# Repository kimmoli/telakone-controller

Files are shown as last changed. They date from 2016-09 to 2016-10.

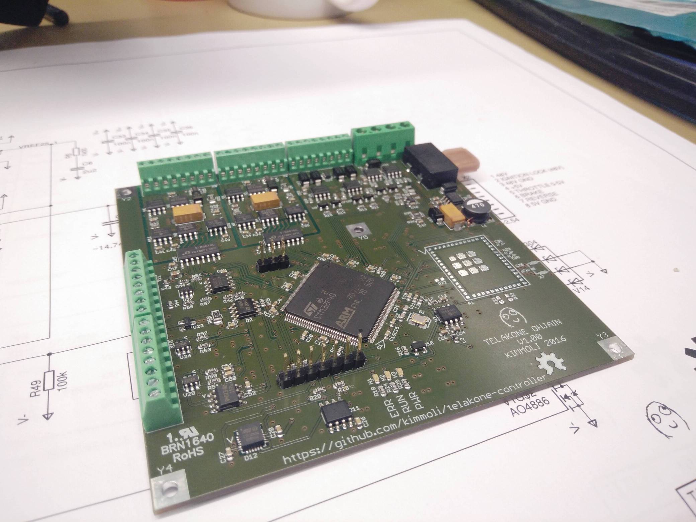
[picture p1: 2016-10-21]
docs/board.jpg

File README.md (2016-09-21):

telakone-controller
===================

STM32F407ZG + CC3100MOD WiFi with external antenna

12V to 3.3V switch mode power supply

Full bridge motor control with current measurement

4x high-side outputs
* PWM capable
* +12V, few amps

Dual isolated eBike motor control
* Throttle control (0-5V output)
* Brake and Reverse (low-side outputs)
* +48V voltage measurement

+12V supply voltage measurement

Temperature sensor

3-Axis accelerometer

Joystick input
* 2 potentiometers
* 2 buttons

Speed sensor inputs
* 2 channels
* for MLX90217 gear tooth sensor

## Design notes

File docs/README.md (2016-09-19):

Documentation
=============

All these are currently propably out of date, just showing off progress.

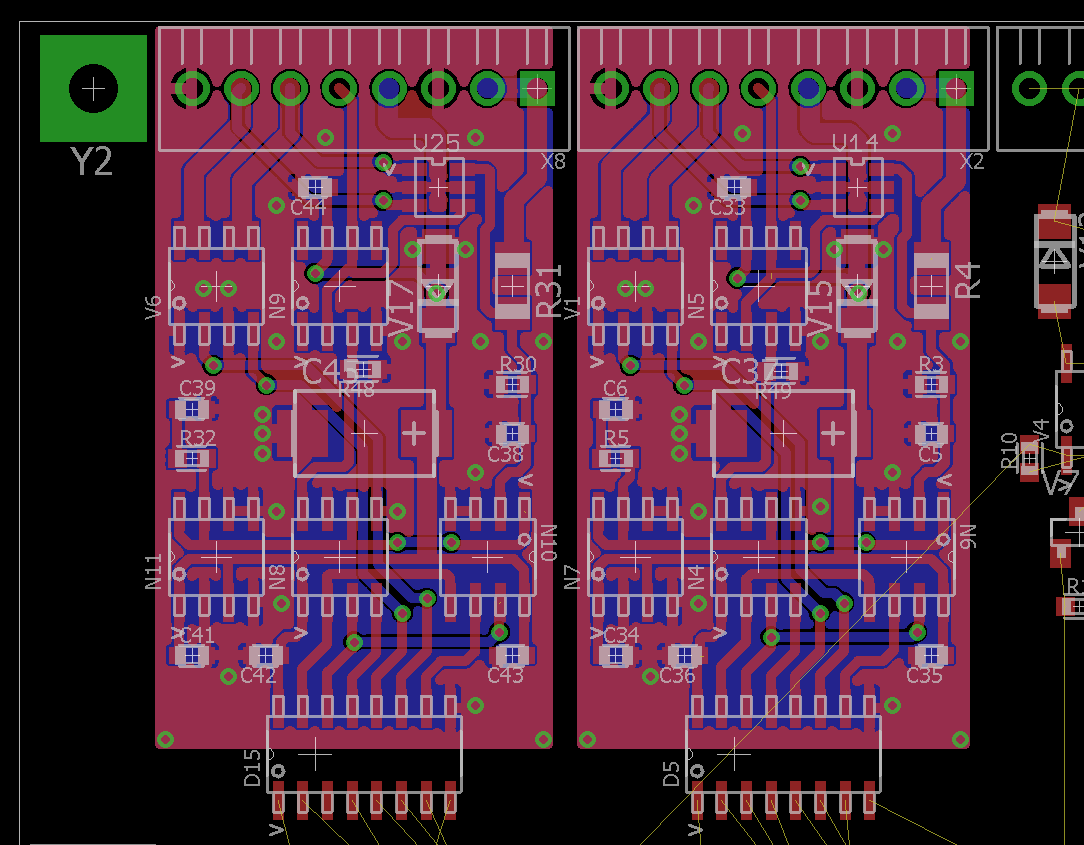
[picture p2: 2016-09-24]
docs/isolaatioryhma-sijoittelu.png

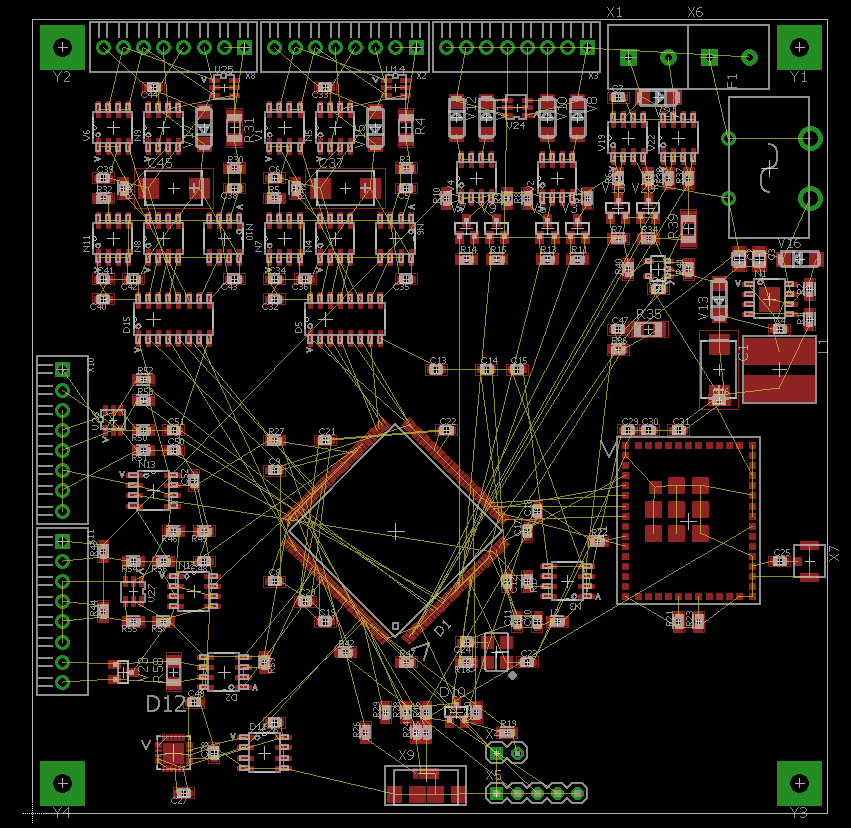
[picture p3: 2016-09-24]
docs/sijoittelu.png

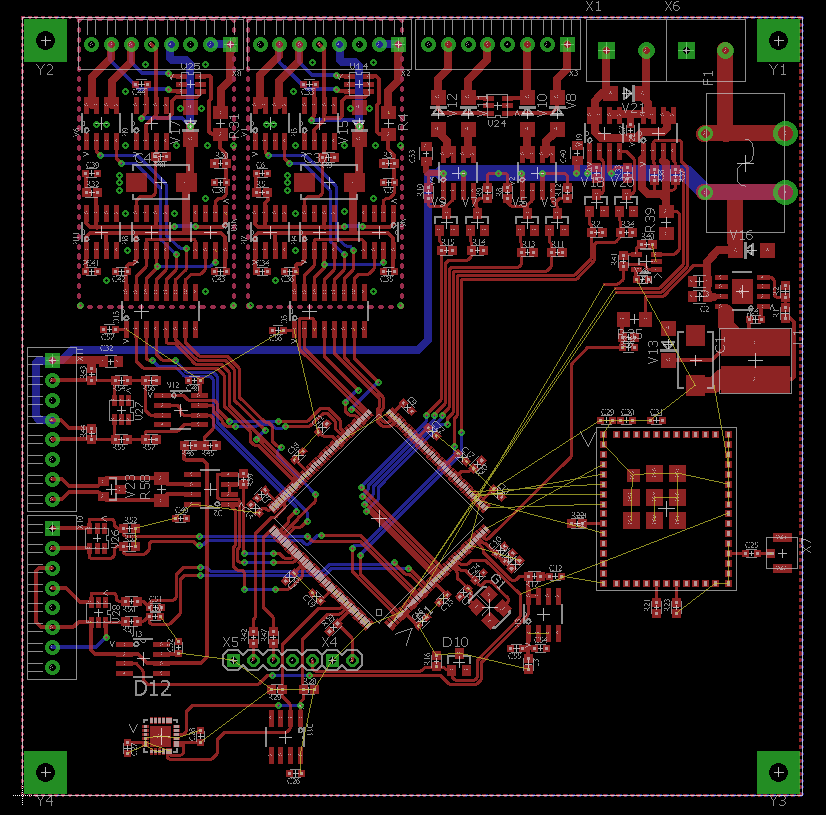
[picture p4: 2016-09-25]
docs/routtausta.png

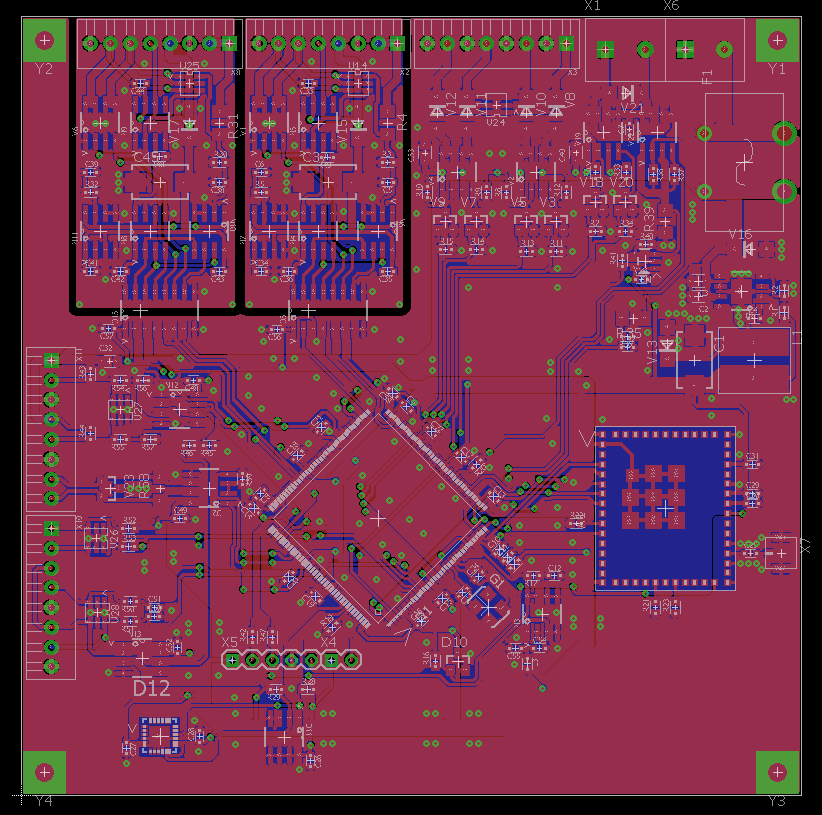
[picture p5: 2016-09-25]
docs/routattu.png

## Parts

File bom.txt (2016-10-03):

Partlist exported from c:/work/OMAT/telakone/telakone.sch at 3.10.2016 20:16

Qty Value           Device          Package               Parts                                                                                                                                                Description                          
2                   TE_RUUVILIITIN2 TE_RUUVILIITIN2       X1, X6                                                                                                                                                                                    
1   10              RES0603         R0603                 R40                                                                                                                                                                                       
2   100k            RES0603         R0603                 R48, R49                                                                                                                                                                                  
30  100n            CAP0603         C0603                 C10, C13, C14, C15, C16, C17, C18, C19, C20, C21, C22, C26, C27, C31, C33, C34, C35, C36, C41, C42, C43, C44, C46, C48, C49, C52, C55, C56, C57, C58                                      
1   10k0            RES0603         R0603                 R1                                                                                                                                                                                        
7   10n             CAP0603         C0603                 C4, C5, C7, C38, C47, C50, C51                                                                                                                                                            
1   10p             CAP0603         C0603                 C25                                                                                                                                                                                       
1   121 1206        RES1206         R1206                 R58                                                                                                                                                                                       
2   19k1 1206       RES1206         R1206                 R4, R31                                                                                                                                                                                   
5   1k00            RES0603         R0603                 R5, R17, R32, R43, R44                                                                                                                                                                    
3   220u 16V D      CPOL-EUCT7343   CT7343                C1, C37, C45                                                                                                                                         POLARIZED CAPACITOR, European symbol 
2   22p             CAP0603         C0603                 C23, C24                                                                                                                                                                                  
1   25MHz           XTAL_3225_SMD   X_3225                G1                                                                                                                                                   CRYSTAL CLOCK OSCILLATORS            
6   2N7002K         2N7002K         SOT23                 V3, V5, V7, V9, V18, V20                                                                                                                                                                  
26  2k00            RES0603         R0603                 R6, R7, R8, R9, R10, R11, R12, R13, R14, R15, R16, R19, R20, R21, R22, R23, R28, R29, R33, R34, R37, R38, R46, R52, R53, R59                                                              
10  2u2             CAP0603         C0603                 C6, C8, C9, C11, C12, C28, C29, C30, C39, C54                                                                                                                                             
5   2u2 50V 0805    CAP0805         C0805                 C2, C3, C32, C40, C53                                                                                                                                                                     
2   30k1            RES0603         R0603                 R54, R55                                                                                                                                                                                  
9   499             RES0603         R0603                 R18, R24, R25, R41, R42, R45, R47, R50, R51                                                                                                                                               
3   5k90            RES0603         R0603                 R2, R56, R57                                                                                                                                                                              
1   5k90 1206       RES1206         R1206                 R35                                                                                                                                                                                       
3   825             RES0603         R0603                 R3, R30, R36                                                                                                                                                                              
3   AO4803A         AO4803A         SOIC8-N_MC            V2, V4, V19                                                                                                                                                                               
3   AO4886          AO4886          SOIC8-N_MC            V1, V6, V22                                                                                                                                                                               
1   AZV3002S        AZV3002S        SOIC8-N_MC            N12                                                                                                                                                                                       
1   CC3100MOD       CC3100MOD       CC3100MOD             A1                                                                                                                                                                                        
8   DAFUG           DAFUG           DAFUG                 U$1, U$3, U$5, U$7, U$9, U$11, U$13, U$15                                                                                                                                                 
1   ERJ-8BWFR010V   RES1206         R1206                 R39                                                                                                                                                                                       
2   ESDA19SC6       ESDAXXSC6       SOT23-6               V24, V27                                                                                                                                                                                  
2   GRN             LEDCHIP-LED0603 CHIP-LED0603          H2, H3                                                                                                                                               LED                                  
1   IIS328DQTR      IIS328DQTR      QFN50P400X400X100-25N D12                                                                                                                                                                                       
2   IND0603         IND0603         R0603                 L2, L3                                                                                                                                                                                    
1   KEYSTONE-3549-2 KEYSTONE-3549-2 KEYSTONE-3549-2       F1                                                                                                                                                                                        
1   LM75BD          LM75BD          SOIC8-N_MC            D11                                                                                                                                                                                       
1   LTC2050CS5      LTC2050CS5      SOT95P280X145-5N      N2                                                                                                                                                                                        
1   MAX3430_SA      MAX3088_SA      SOIC8-N_MC            D2                                                                                                                                                                                        
3   MCP1501/SN      MCP1501/SN      SOIC8-N_MC            N3, N7, N11                                                                                                                                                                               
2   MCP3201/SN      MCP3201/SN      SOIC8-N_MC            N6, N10                                                                                                                                                                                   
2   MCP4921/SN      MCP4921/SN      SOIC8-N_MC            N4, N8                                                                                                                                                                                    
5   MPT0.5/8-2.54   MPT0.5/8-2.54   MPT0.5/8-2.54         X2, X3, X8, X10, X11                                                                                                                                                                      
1   PIIKKIRIMA-2    PIIKKIRIMA-2    PIIKKIRIMA-2          X4                                                                                                                                                                                        
1   PIIKKIRIMA-3    PIIKKIRIMA-3    PIIKKIRIMA-3          X9                                                                                                                                                                                        
1   PIIKKIRIMA-5    PIIKKIRIMA-5    PIIKKIRIMA-5          X5                                                                                                                                                                                        
5   PTH2.6-5.5SQ    PTH2.6-5.5SQ    PTH-2.6-5.5SQ         Y1, Y2, Y3, Y4, Y5                                                                                                                                                                        
1   RED             LEDCHIP-LED0603 CHIP-LED0603          H1                                                                                                                                                   LED                                  
1   RT9818C-29GV    RT9818C-29GV    SOT23                 D10                                                                                                                                                                                       
2   SI8661-IS1      SI8661-IS1      SOIC16-N              D5, D15                                                                                                                                                                                   
5   SK34A           SK34A           DO214AC               V8, V10, V11, V12, V13                                                                                                                                                                    
1   SM712           SM712           SOT23                 V23                                                                                                                                                                                       
1   SMAJ20A         SMAJXXA         DO214AC               V16                                                                                                                                                                                       
1   SMAJ20CA        SMAJXXCA        DO214AC               V21                                                                                                                                                                                       
2   SMAJ5.0A        SMAJXXA         DO214AC               V15, V17                                                                                                                                                                                  
1   STM32F407ZG     STM32F407ZG     LQFP-144              D1                                                                                                                                                                                        
1   TPS5430DDA      TPS5430DDA      SOIC8-N-EP            N1                                                                                                                                                                                        
3   TS921IDT        TS921IDT        SOIC8-N_MC            N5, N9, N13                                                                                                                                                                               
1   U.FL-R-SMT-1    U.FL-R-SMT-1    U.FL-R-SMT-1          X7                                                                                                                                                                                        
1   VLP8040-47U     VLP8040-47U     VLP8040               L1                                                                                                                                                                                        
4   WURTH 82402304  ESDAXXSC6       SOT23-6               V14, V25, V26, V28

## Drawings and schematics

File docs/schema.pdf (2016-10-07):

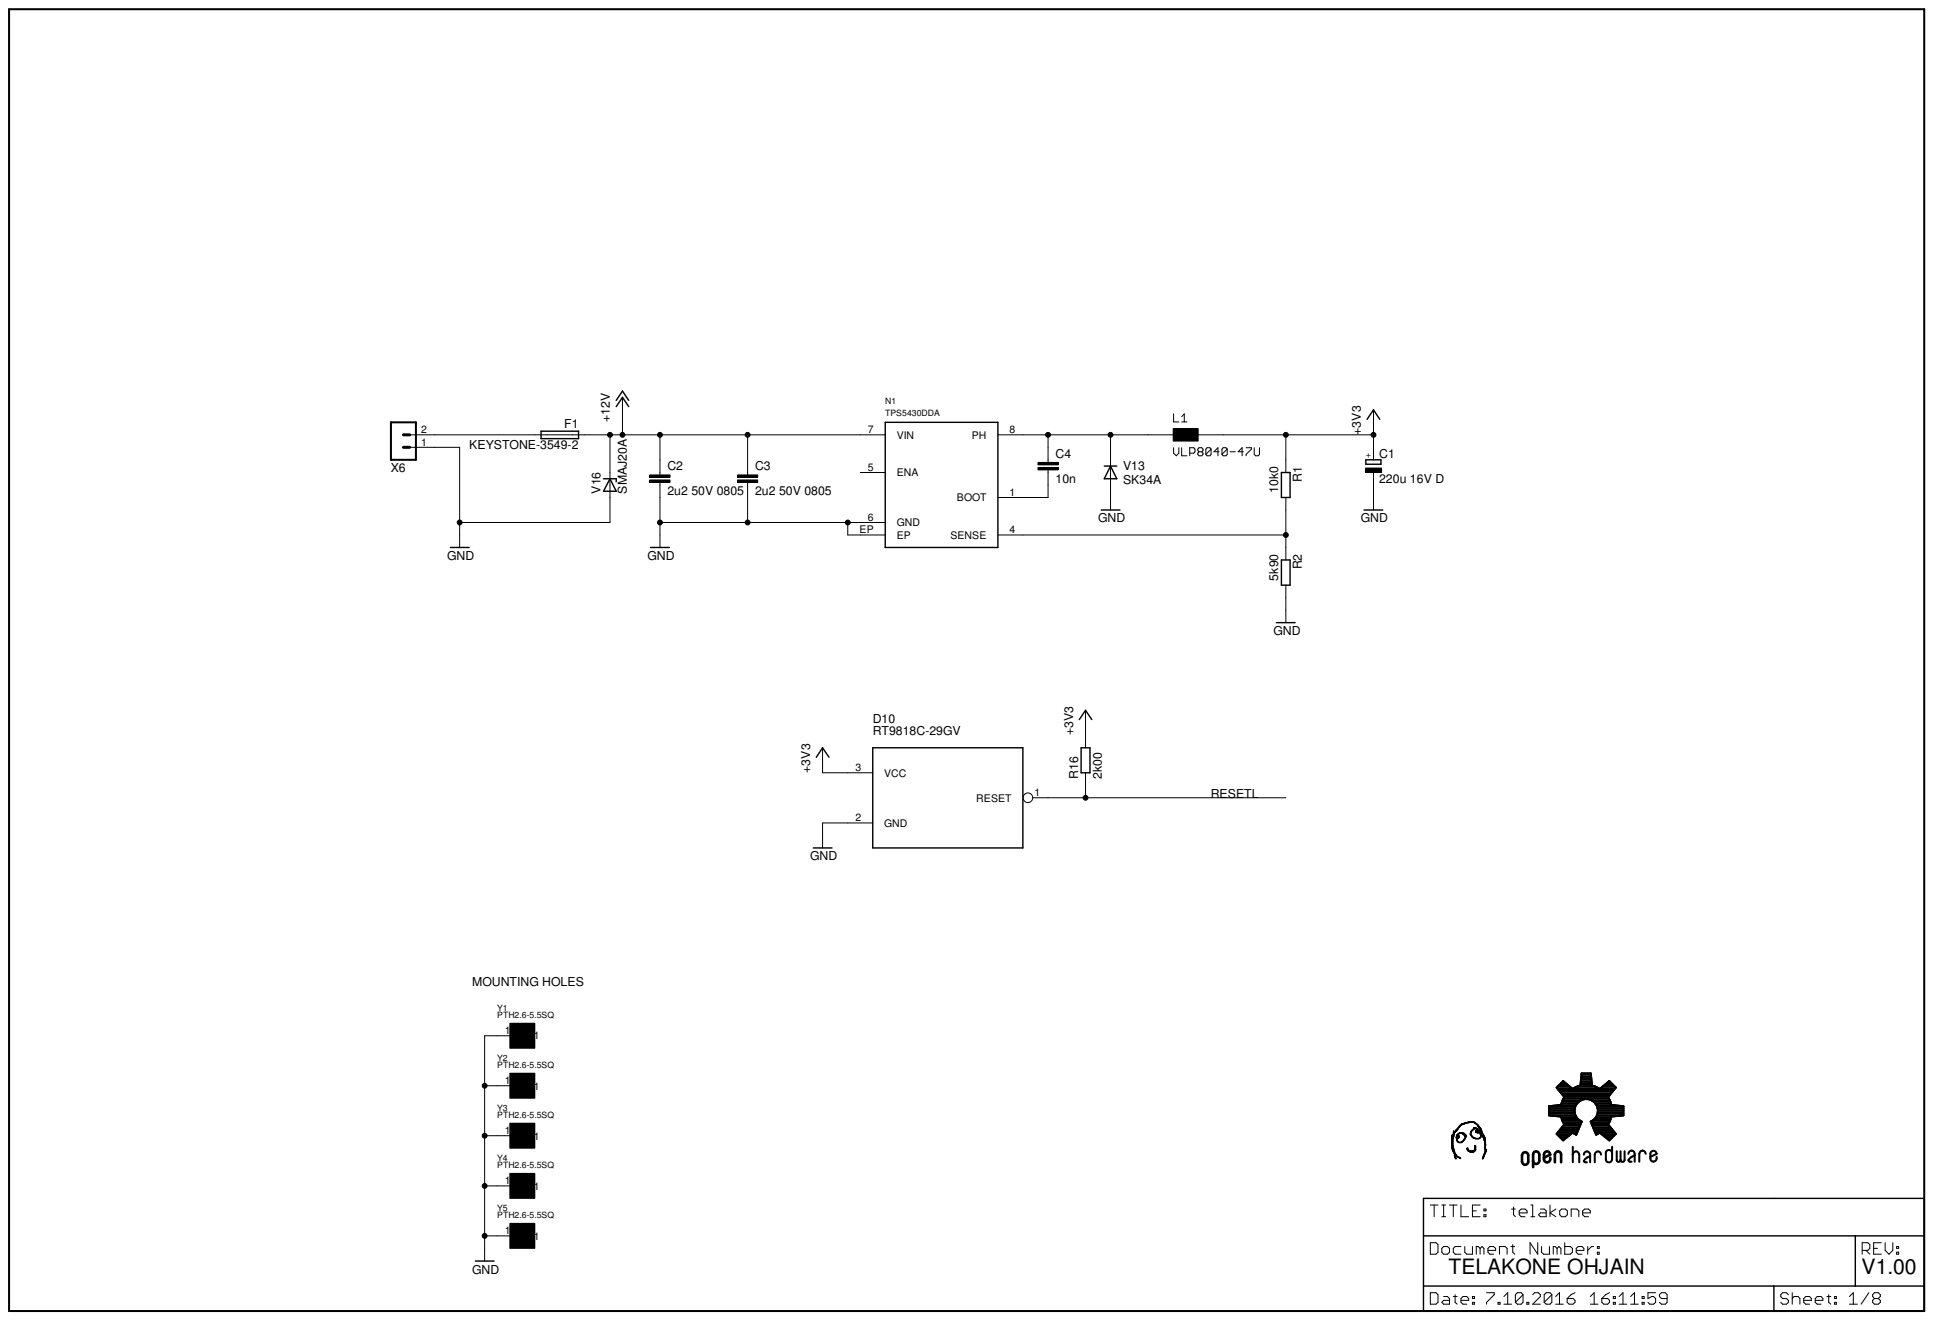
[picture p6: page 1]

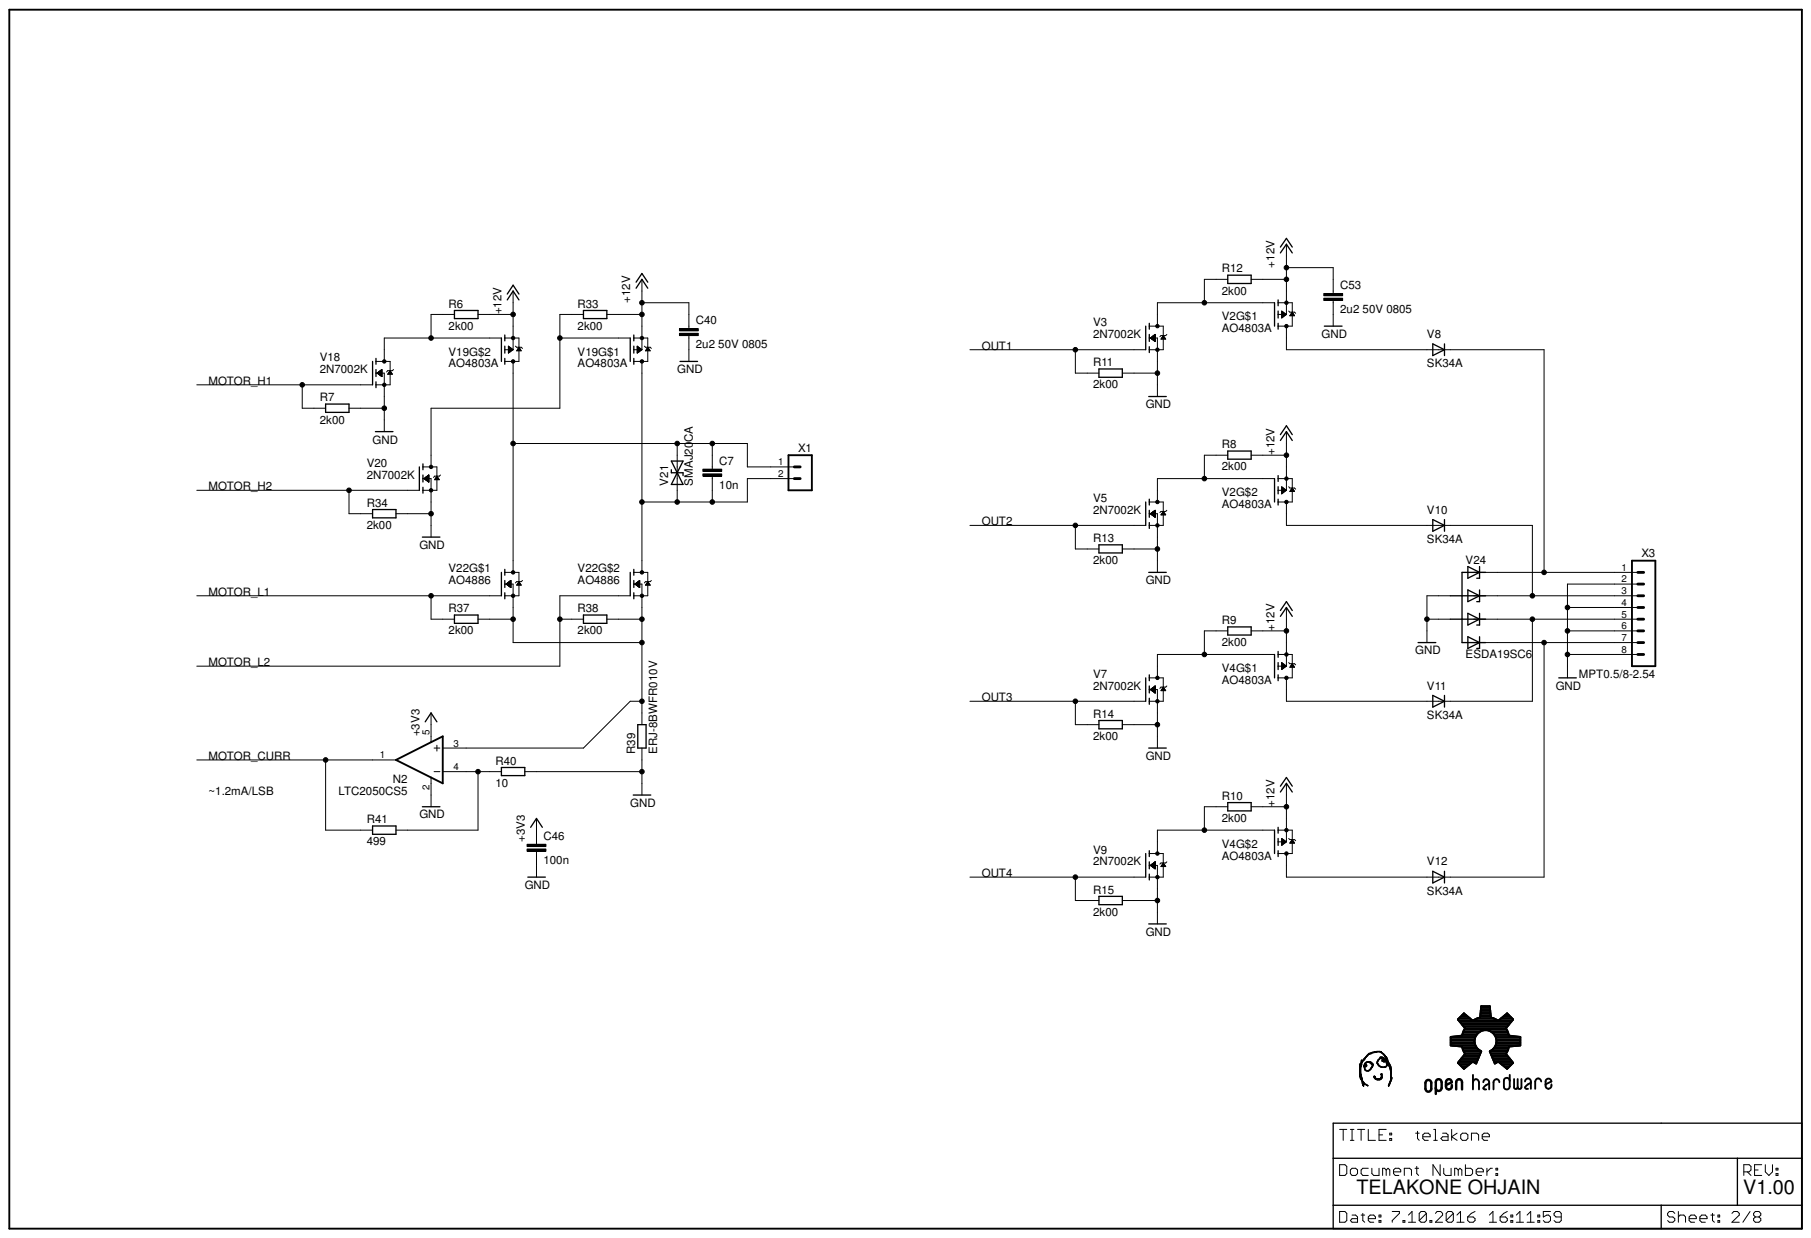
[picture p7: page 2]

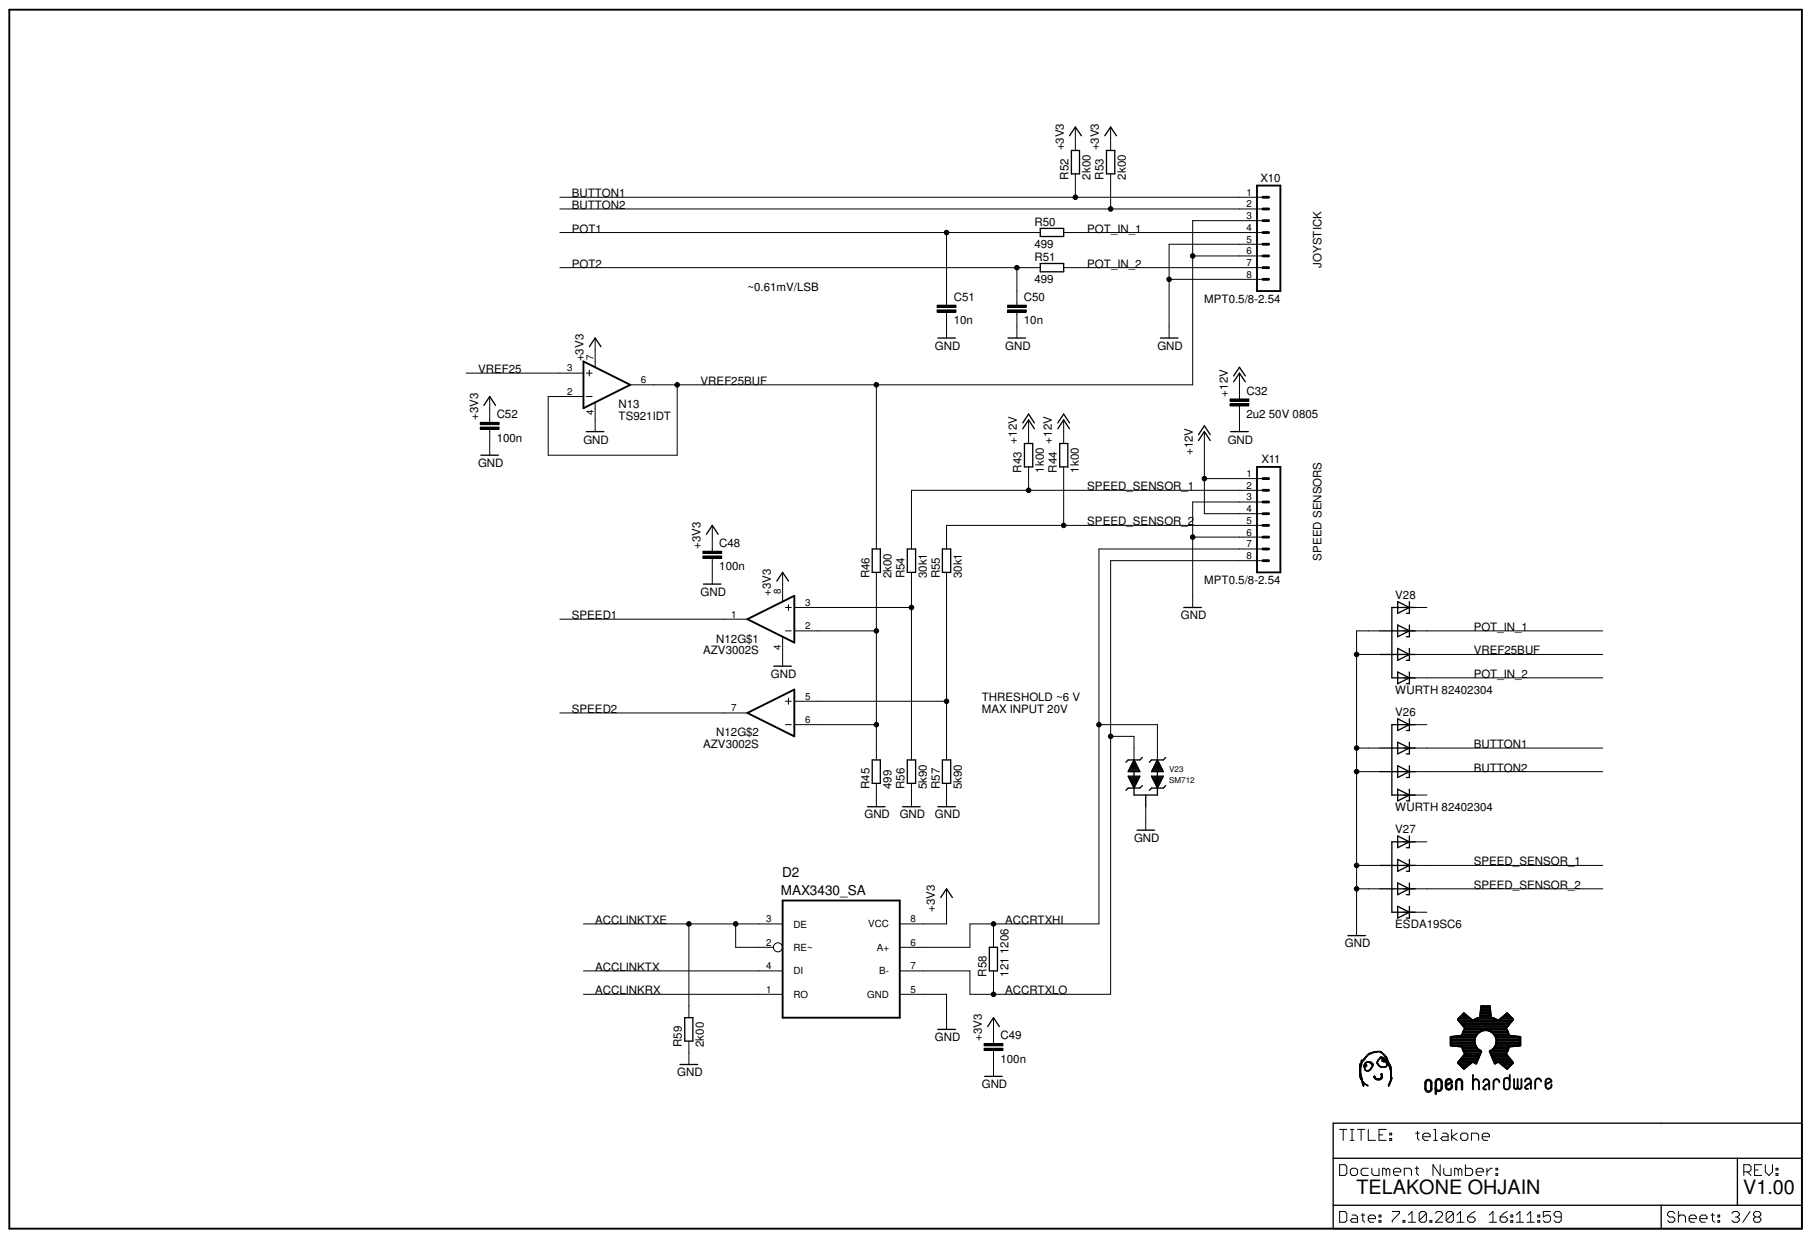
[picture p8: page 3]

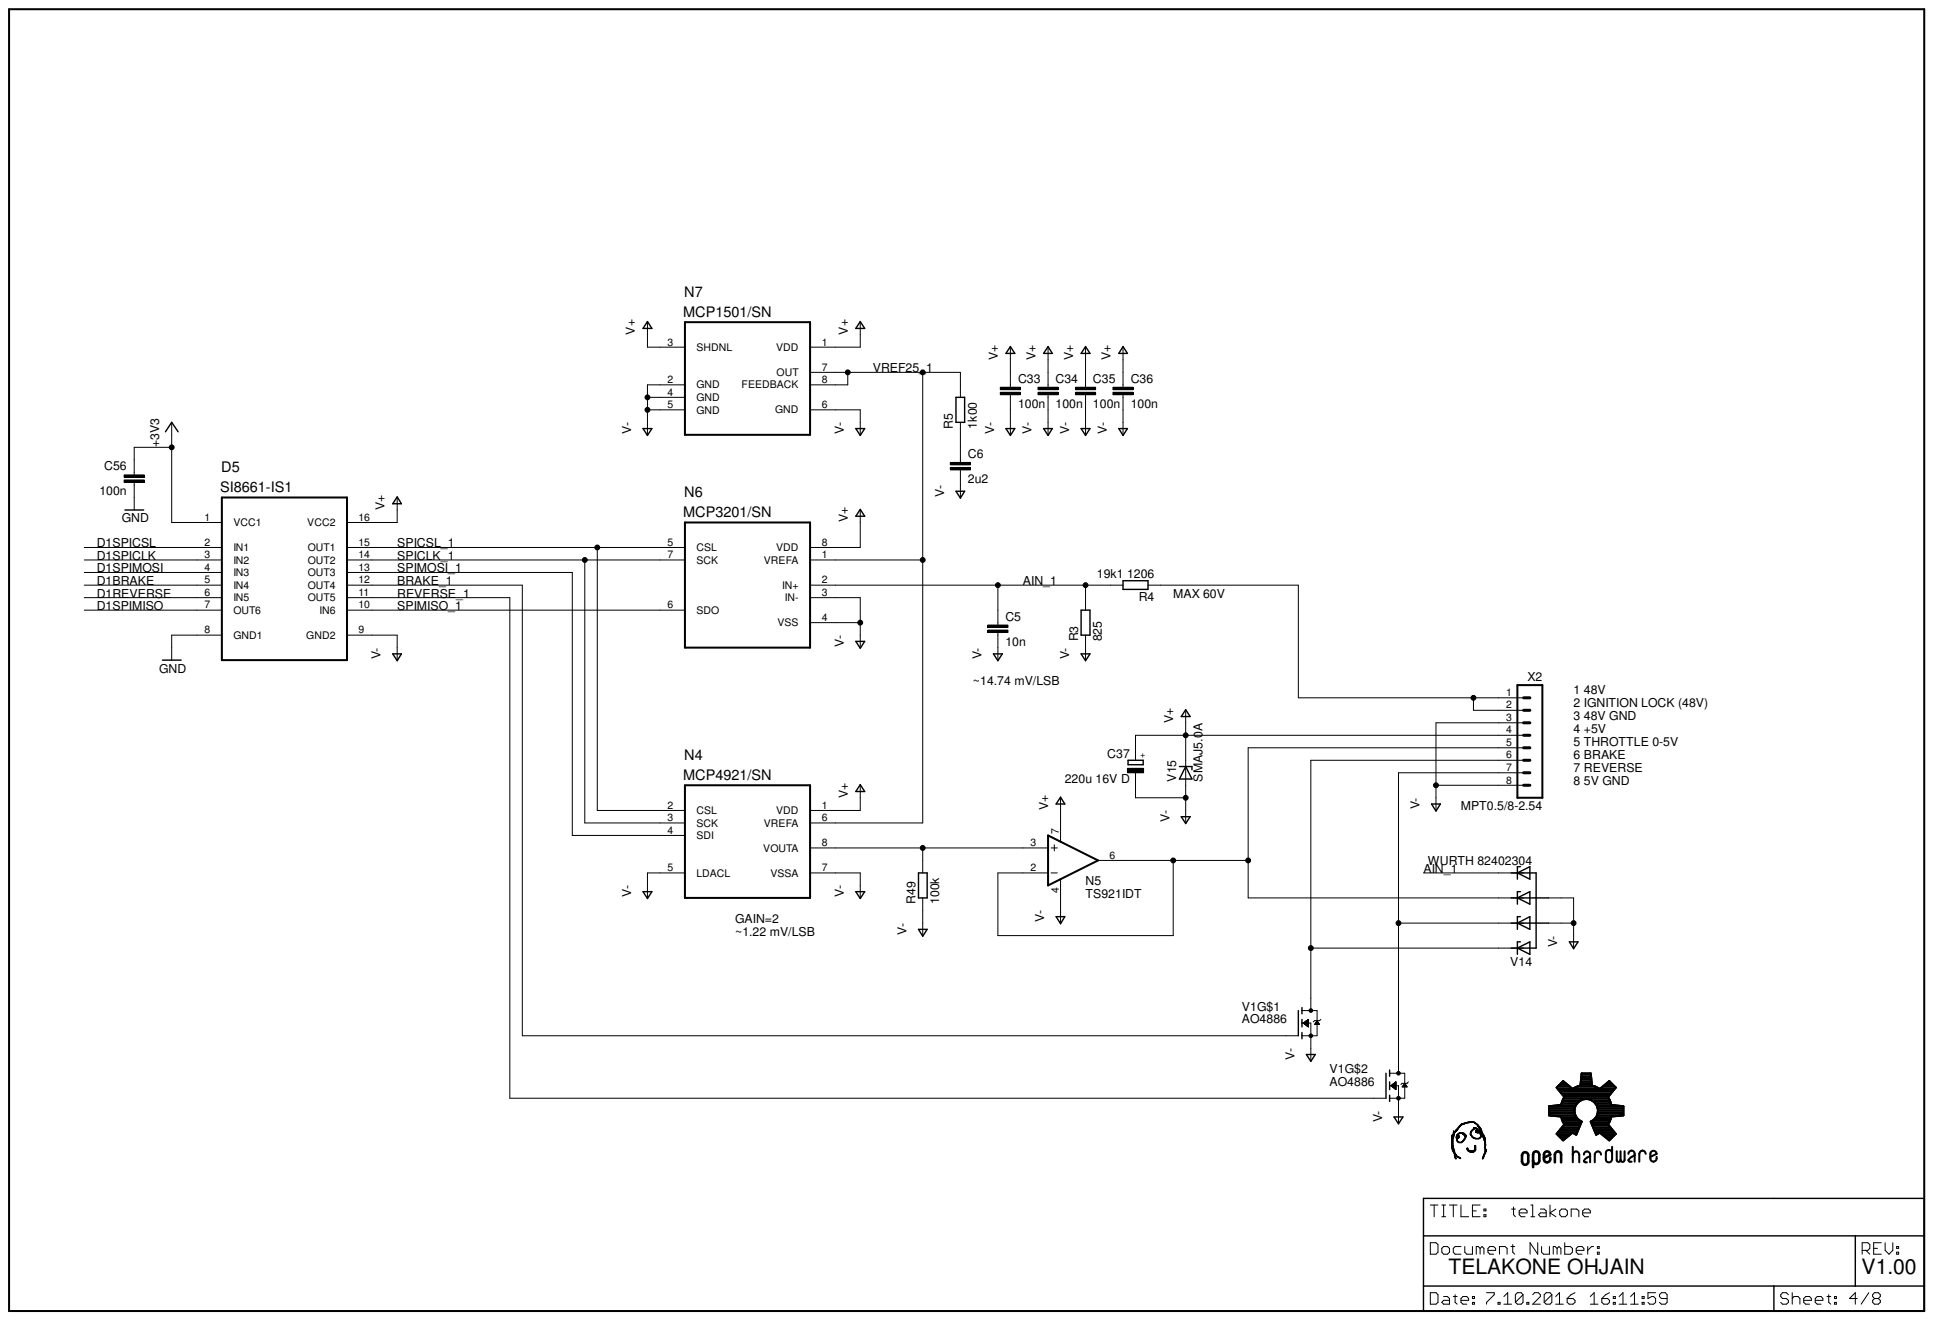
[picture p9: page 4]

SPICLK_1 | | 1
SPIMOSI_1 | 6 | | 2

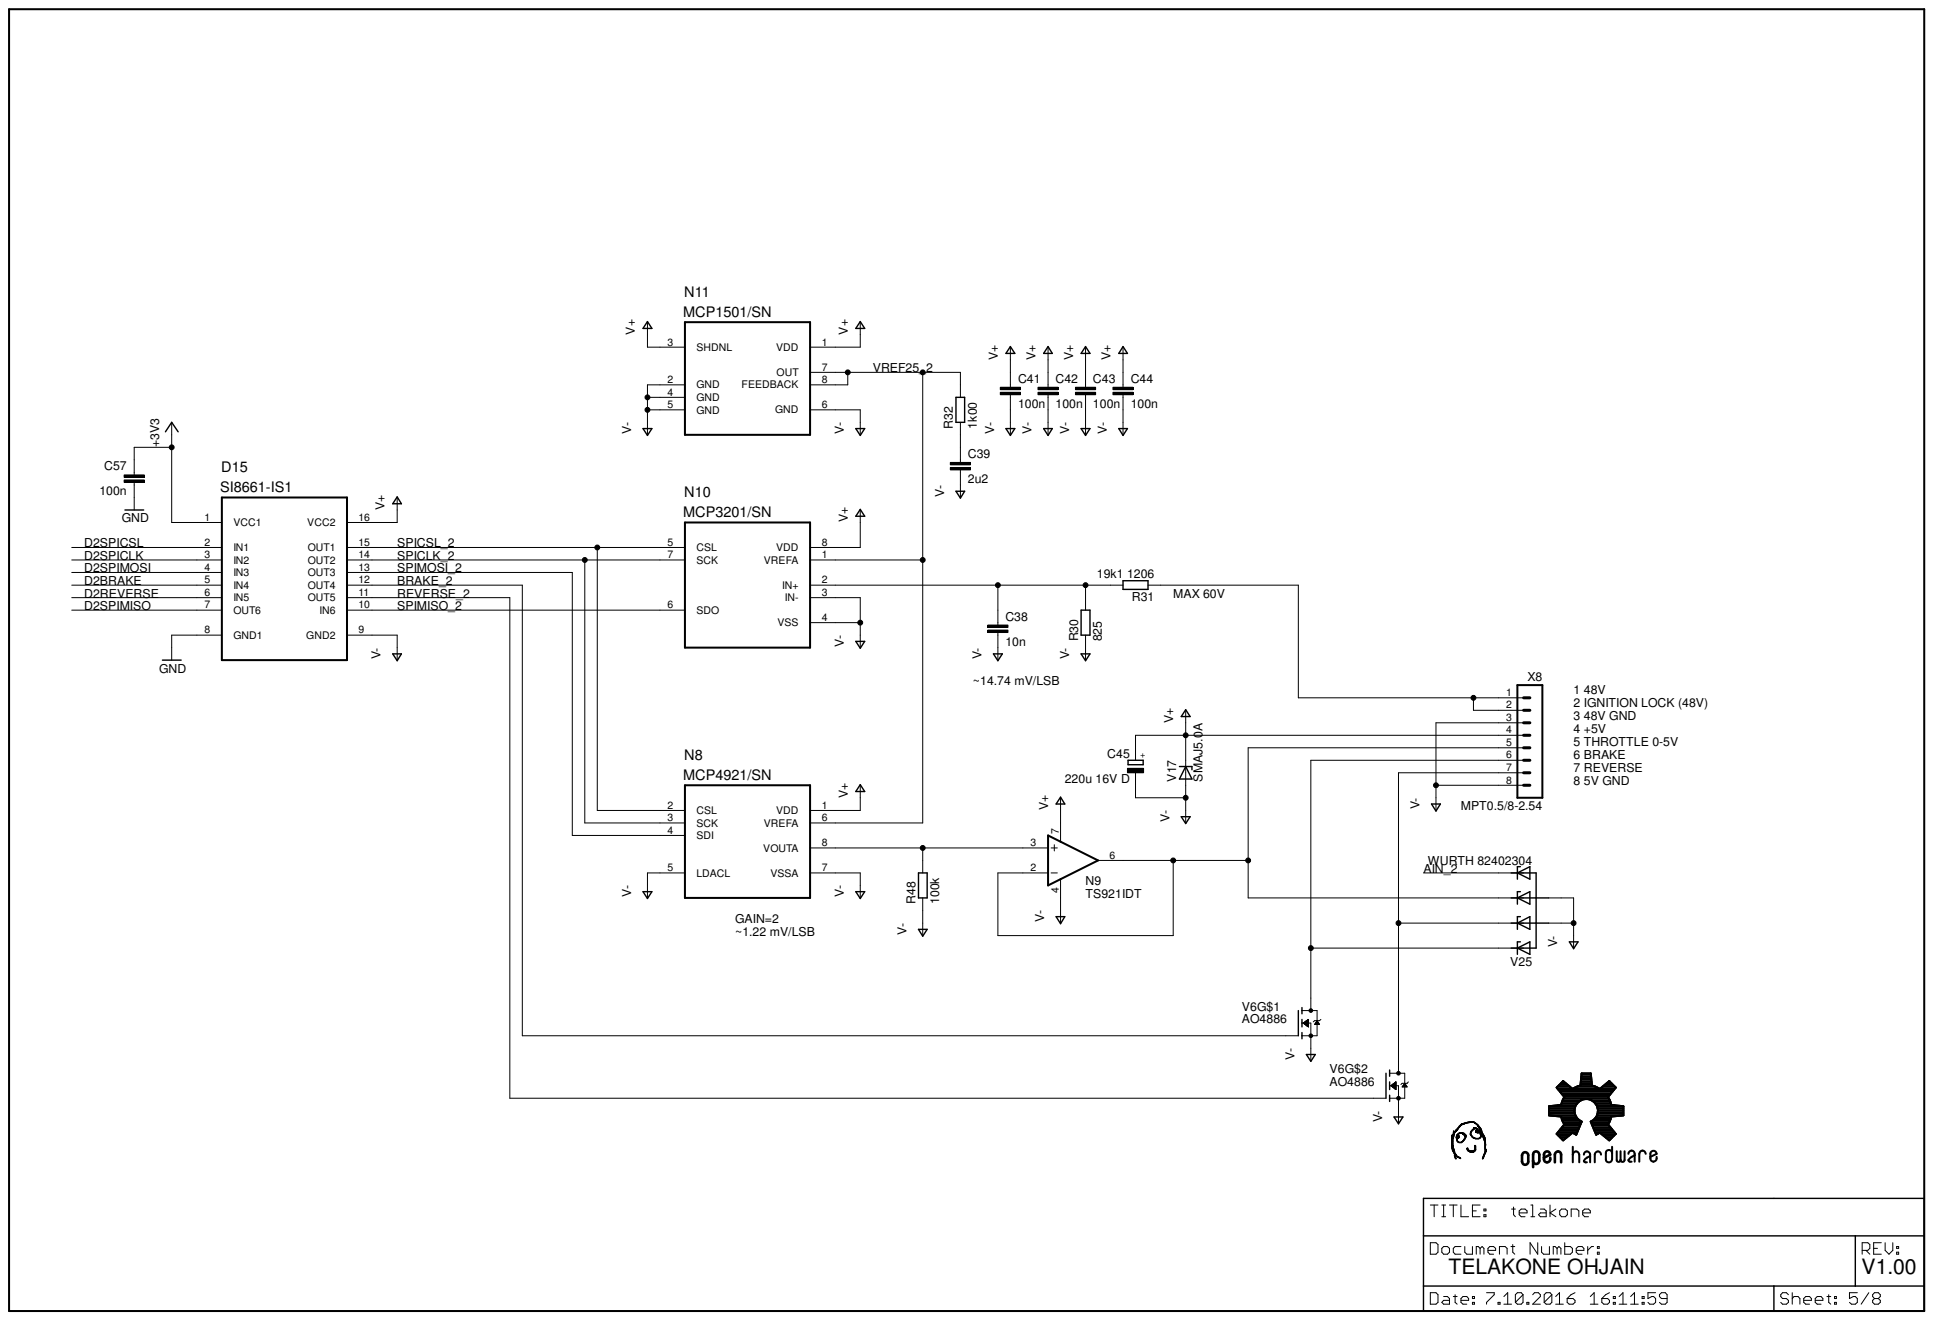
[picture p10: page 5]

SPICLK_2 | | 1
SPIMOSI_2 | 6 | | 2

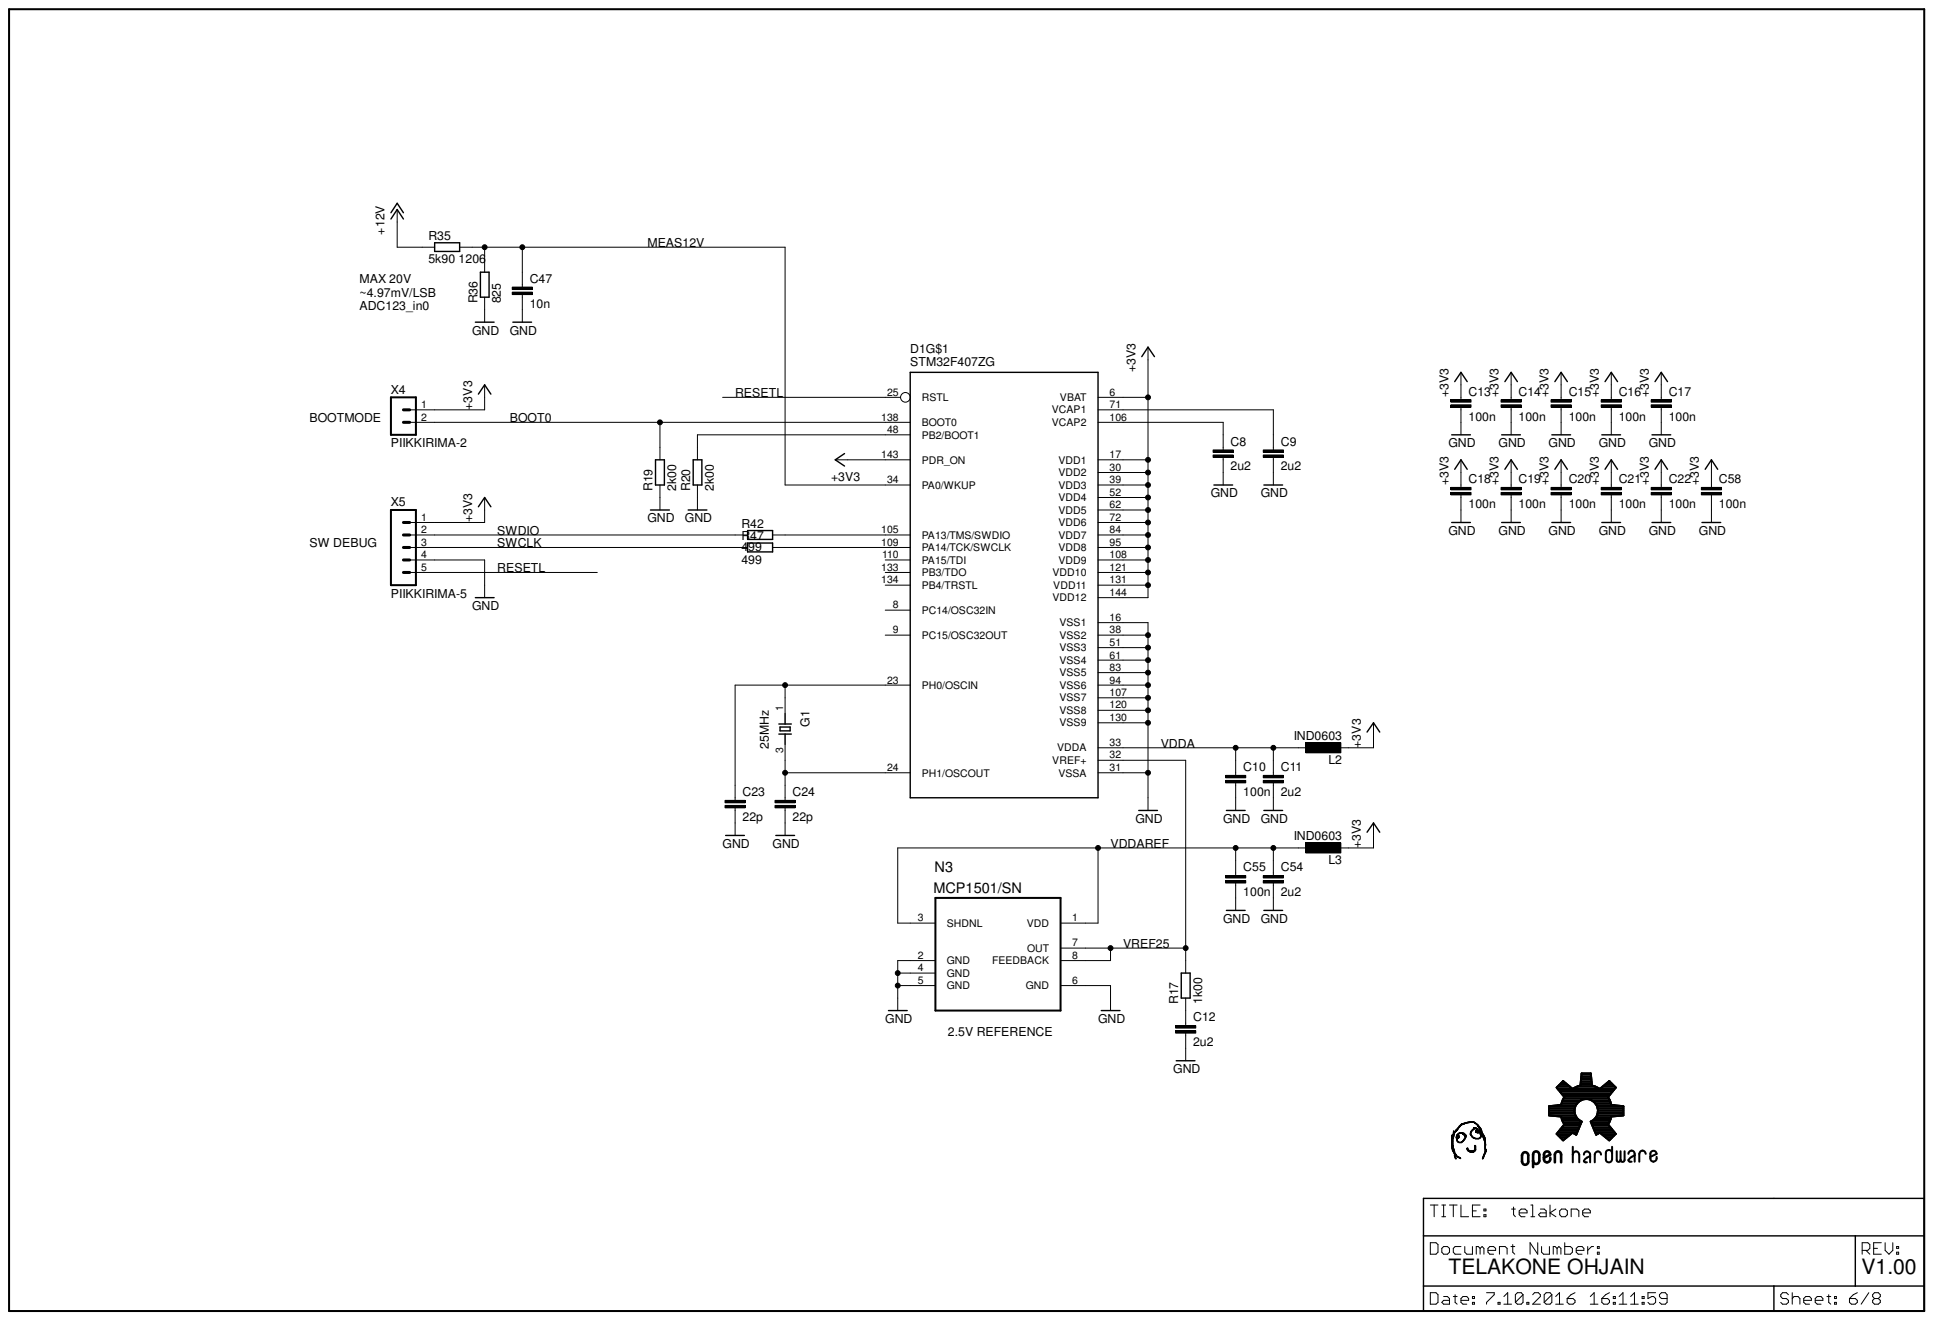
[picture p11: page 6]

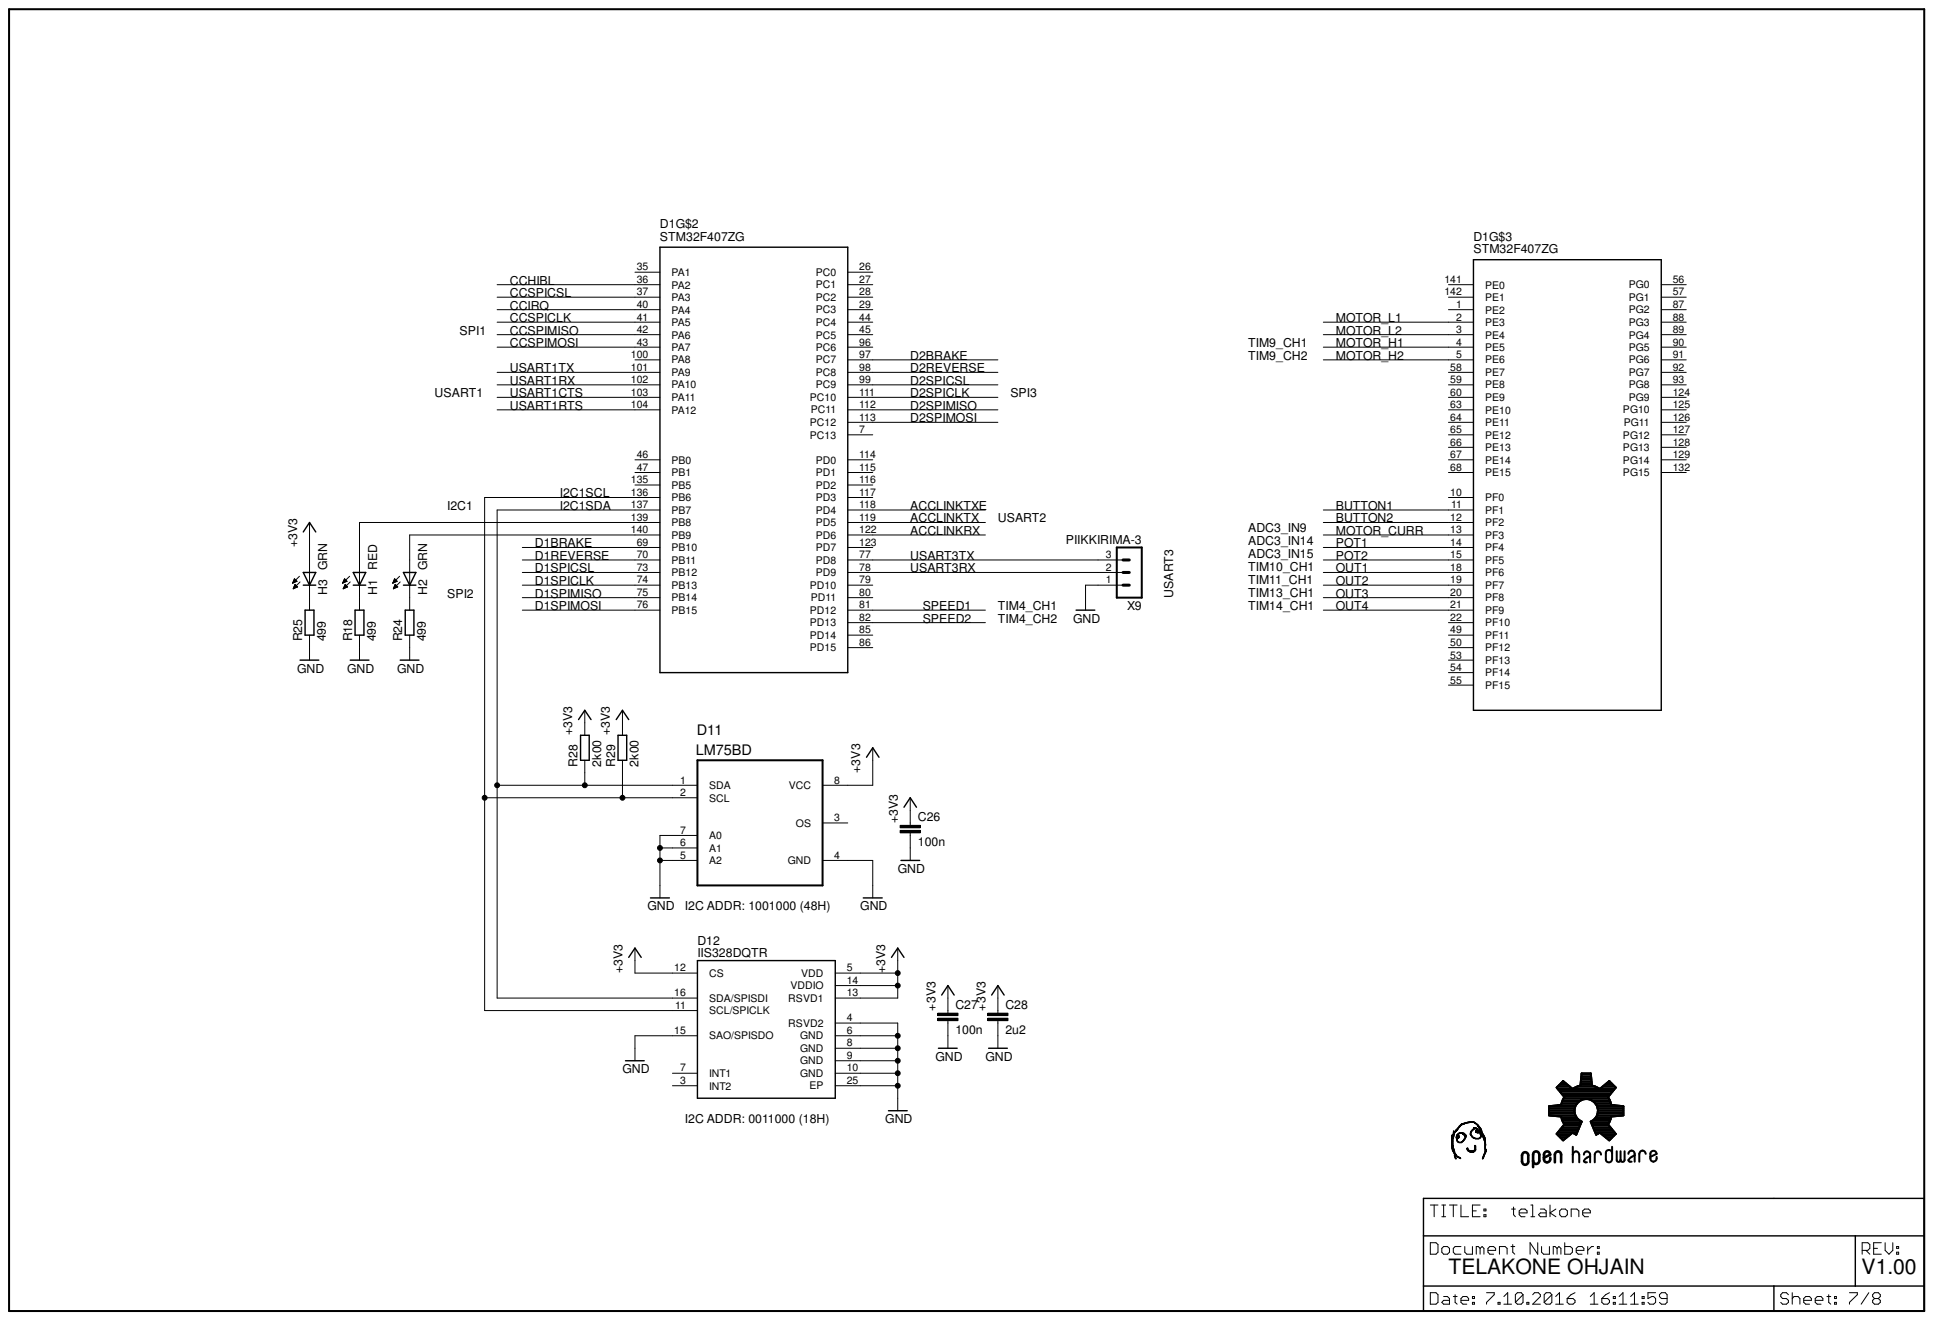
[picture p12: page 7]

PB9 140
PB10 69 PB11 70 PB12 73 PB13 74 PB14 75 PB15 76

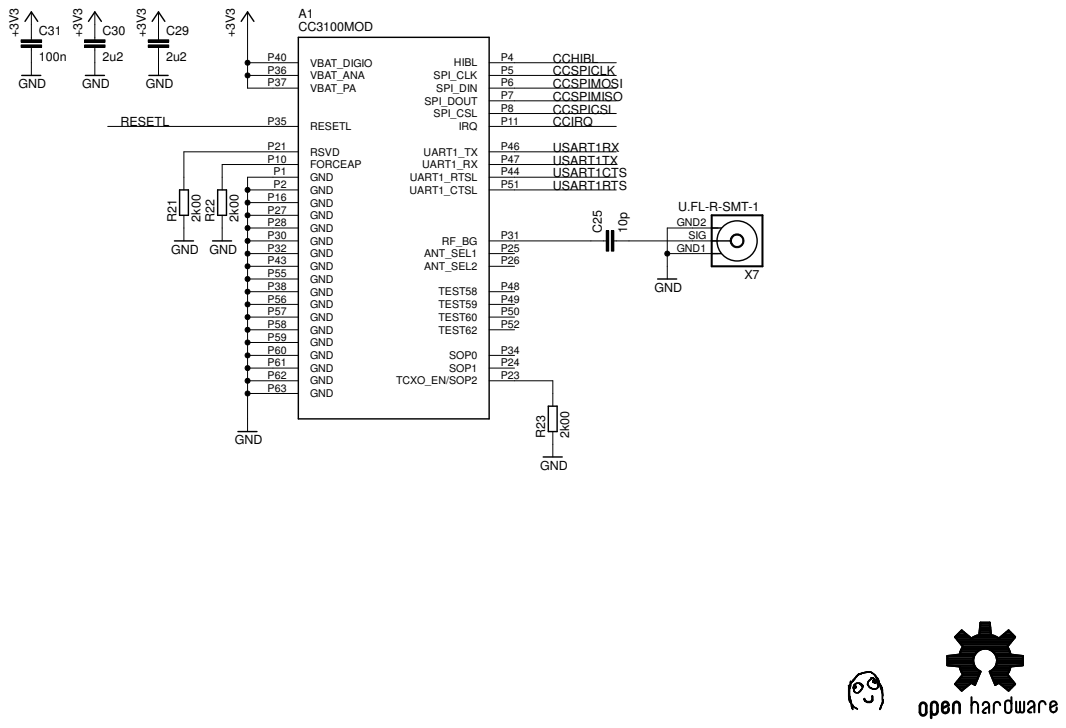
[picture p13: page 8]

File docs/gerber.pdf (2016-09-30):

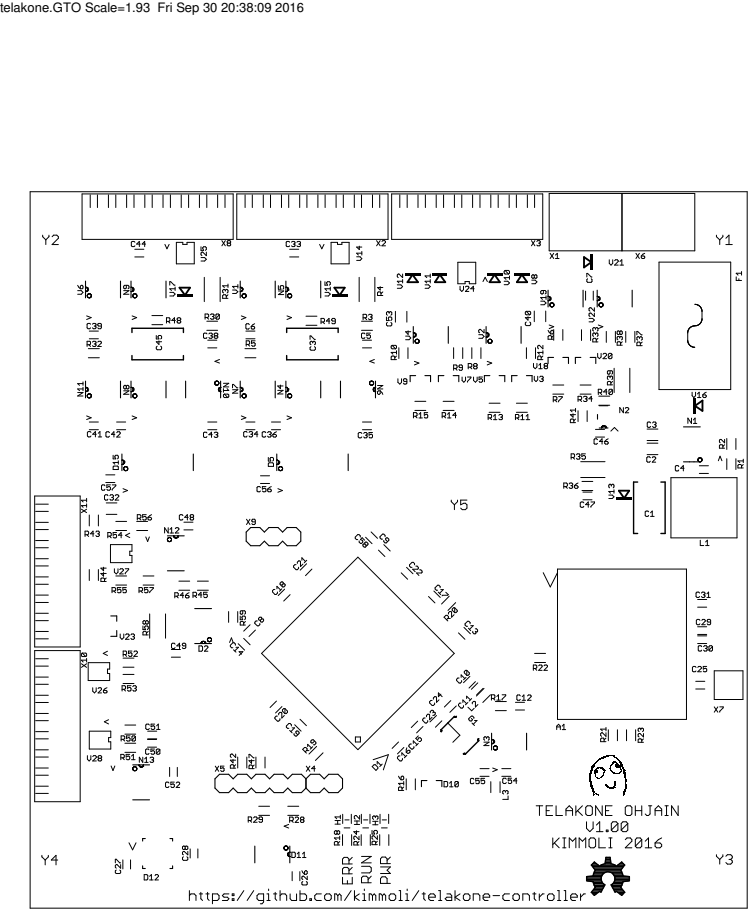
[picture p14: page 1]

telakone.GTO Scale=1.93 Fri Sep 30 20:38:09 2016

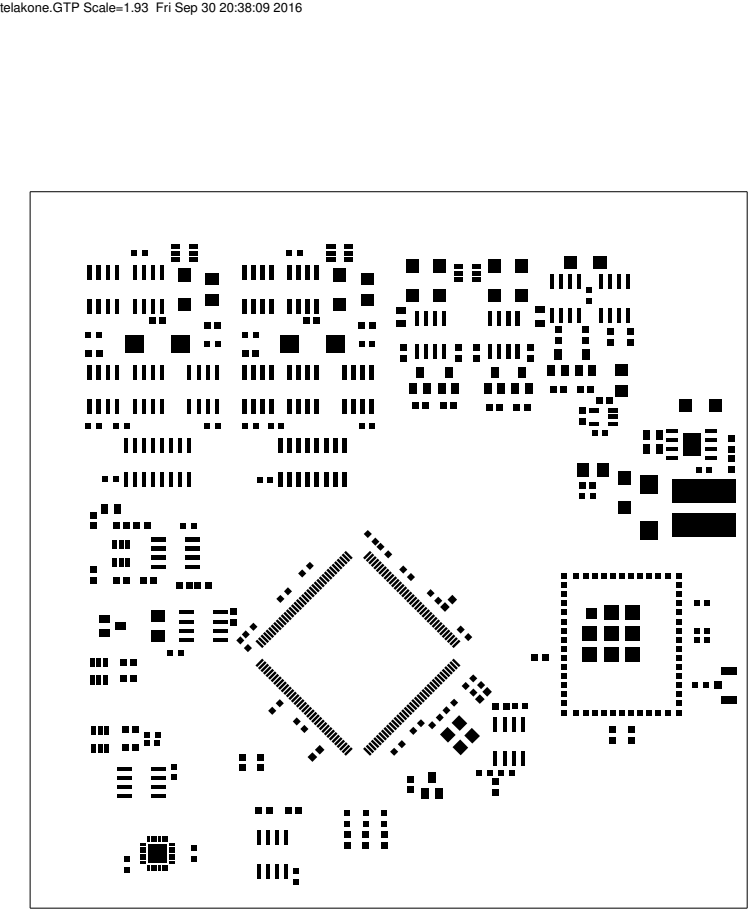
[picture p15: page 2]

telakone.GTP Scale=1.93 Fri Sep 30 20:38:09 2016

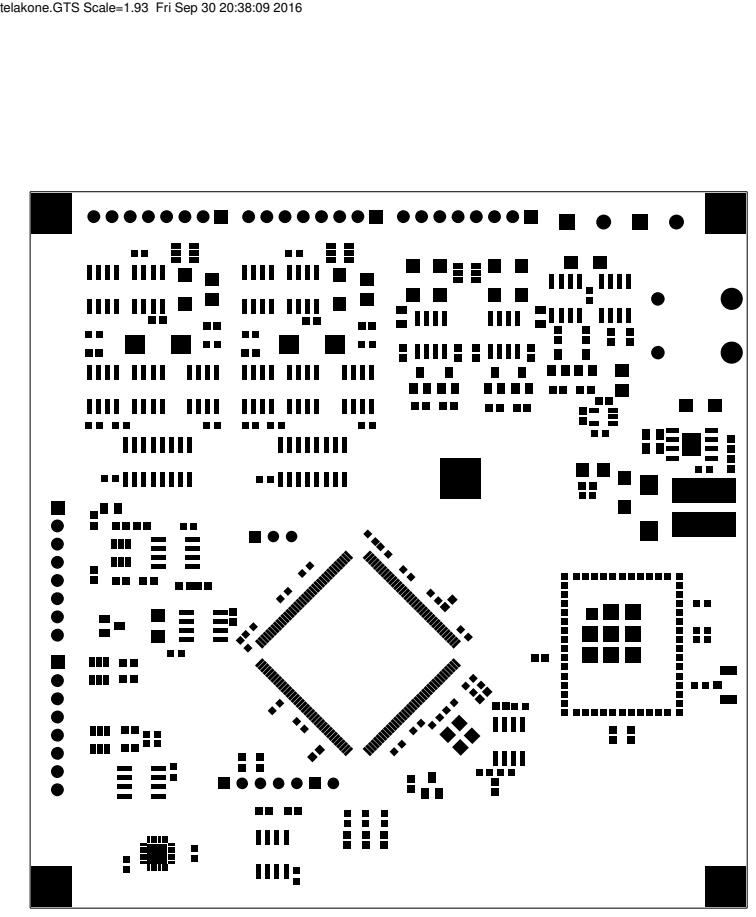
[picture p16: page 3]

telakone.GTS Scale=1.93 Fri Sep 30 20:38:09 2016

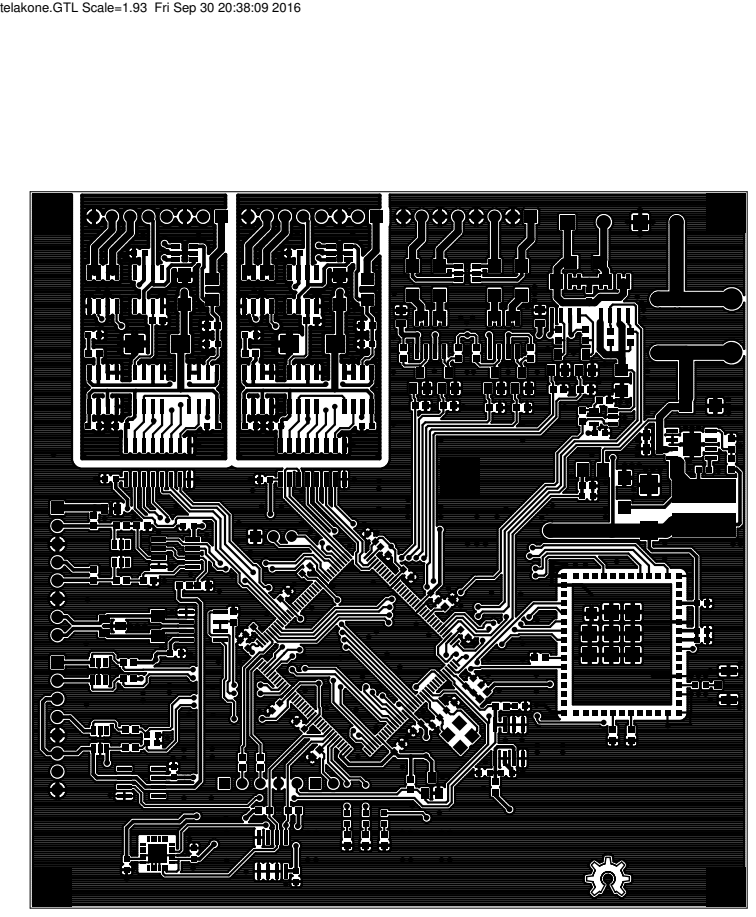
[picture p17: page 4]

telakone.GTL Scale=1.93 Fri Sep 30 20:38:09 2016


telakone.GBL Scale=1.93 Fri Sep 30 20:38:09 2016


telakone.GBS Scale=1.93 Fri Sep 30 20:38:09 2016

telakone.GBP Scale=1.93 Fri Sep 30 20:38:09 2016 telakone.GBO Scale=1.93 Fri Sep 30 20:38:09 2016


telakone.DRD Scale=1.93 Fri Sep 30 20:38:09 2016

telakone.GKO Scale=1.93 Fri Sep 30 20:38:09 2016


telakone.TXT Scale=1.93 Fri Sep 30 20:38:09 2016

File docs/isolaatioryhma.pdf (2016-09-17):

## MCP1501/SN

N7


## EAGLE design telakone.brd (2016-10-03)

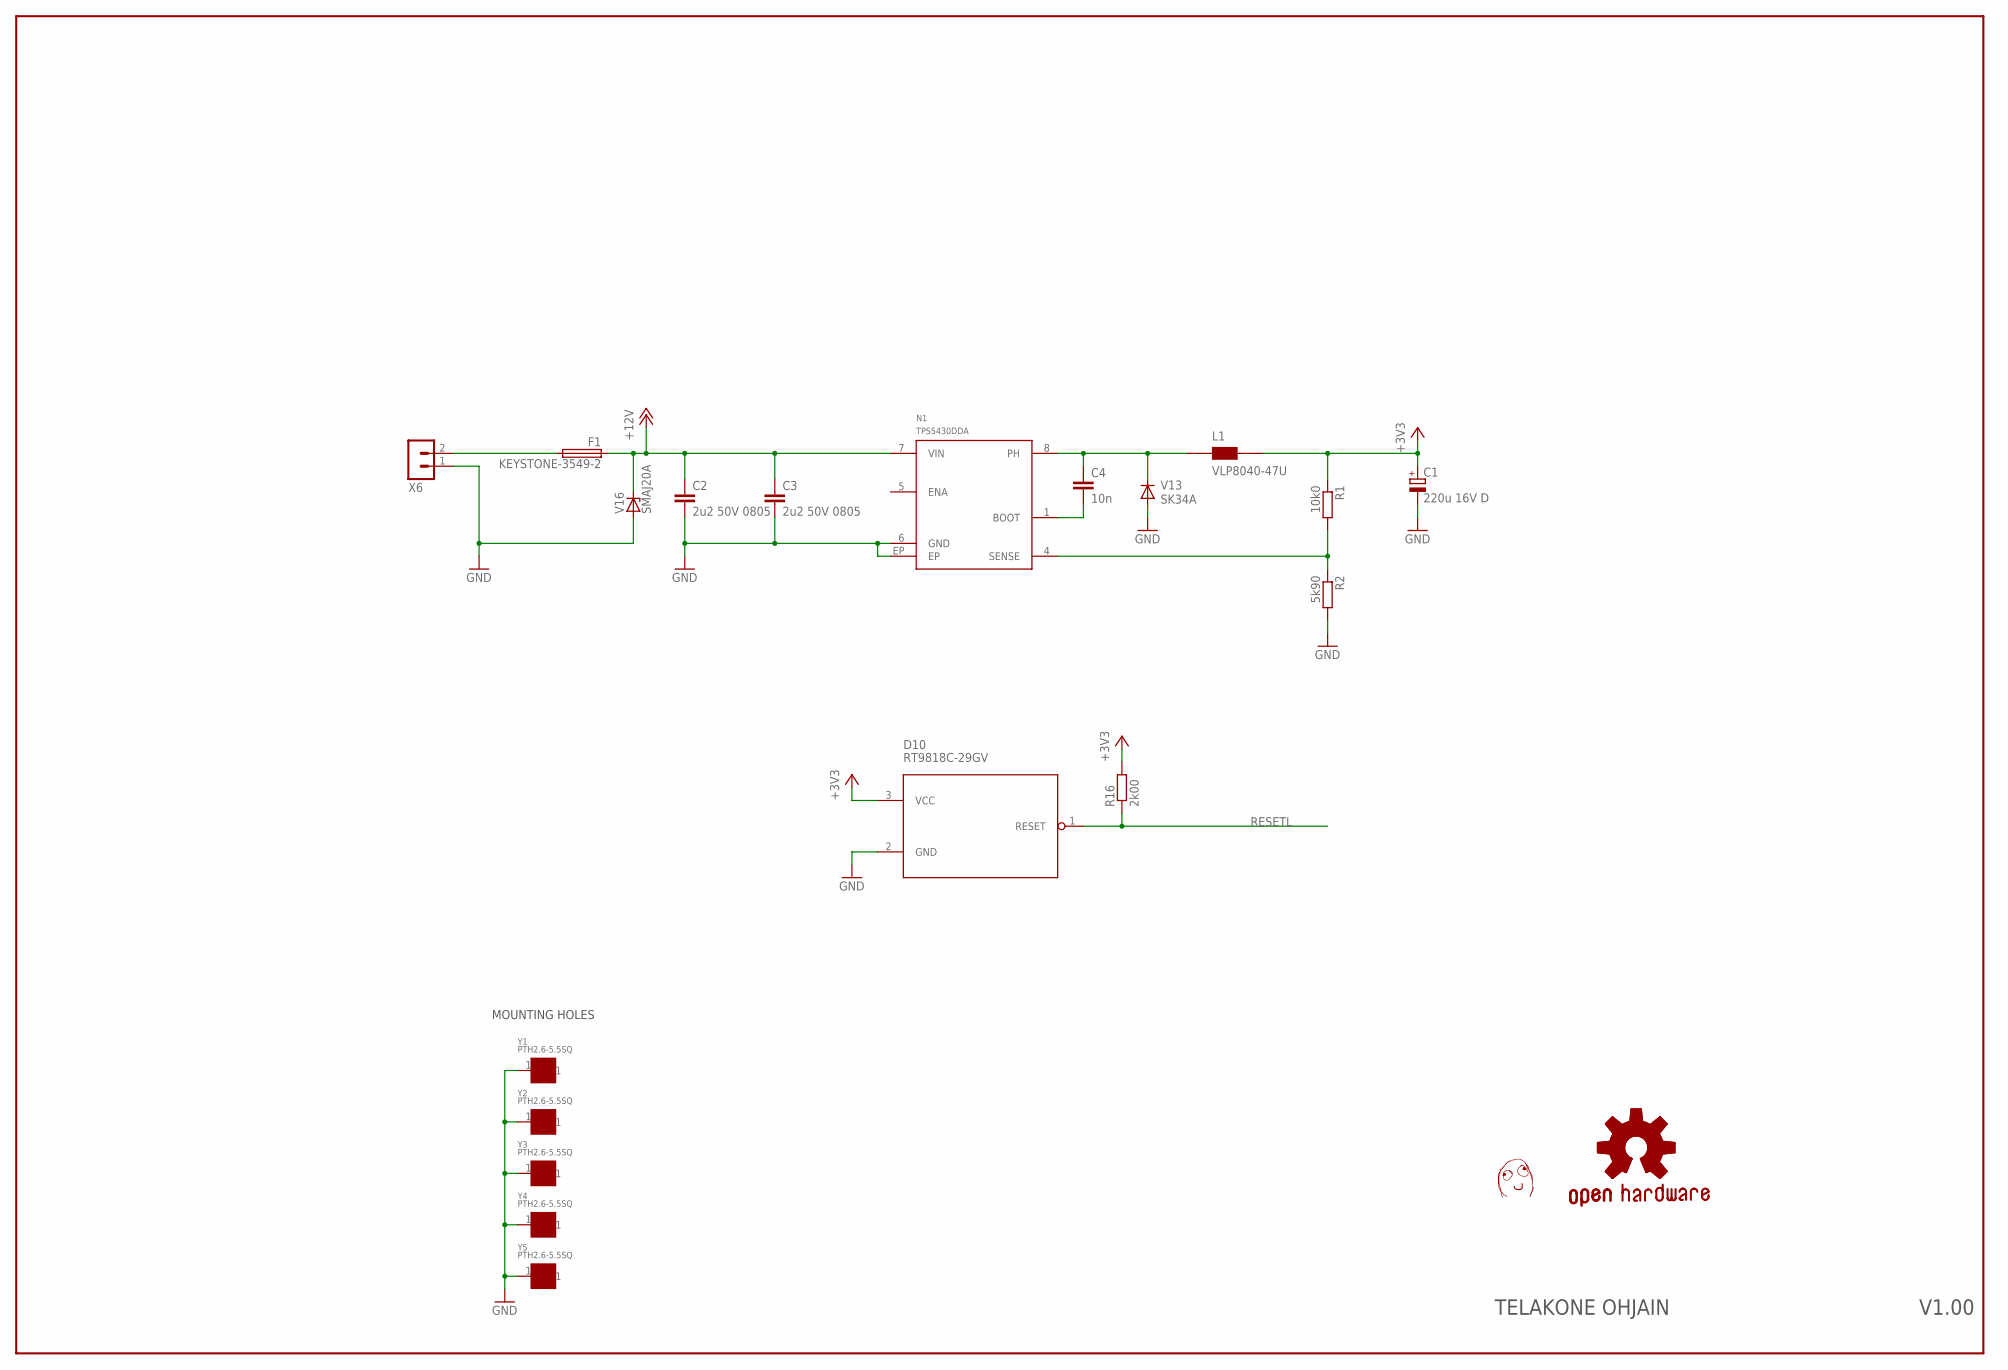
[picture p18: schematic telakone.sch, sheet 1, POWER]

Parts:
C1: 220u 16V D; CT7343
C2, C3: 2u2 50V 0805; C0805
C4: 10n; C0603
D10: RT9818C-29GV; SOT23
F1: KEYSTONE-3549-2
L1: VLP8040-47U; VLP8040
N1: TPS5430DDA; SOIC8-N-EP
R1: 10k0; R0603
R2: 5k90; R0603
R16: 2k00; R0603
U$1: DAFUG
V13: SK34A; DO214AC
V16: SMAJ20A; DO214AC
X6: TE_RUUVILIITIN2
Y1, Y2, Y3, Y4, Y5: PTH2.6-5.5SQ; PTH-2.6-5.5SQ

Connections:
+3V3: C1.+, D10.3 (VCC), L1.2 (B), R1.1, R16.2; also elsewhere on the board
+12V: C2.1, C3.1, F1.1, F1.4 (1), N1.7 (VIN), V16.C; also elsewhere on the board
GND: C1.-, C2.2, C3.2, D10.2 (GND), N1.6 (GND), N1.EP, R2.2, V13.A, V16.A, X6.1, Y1.1, Y2.1, Y3.1, Y4.1, Y5.1; also elsewhere on the board
unnamed: C4.1, L1.1 (A), N1.8 (PH), V13.C
unnamed: C4.2, N1.1 (BOOT)
unnamed: N1.4 (SENSE), R1.2, R2.1
unnamed: F1.2, F1.3 (2), X6.2
RESETL: D10.1 (RESET), R16.1; also elsewhere on the board

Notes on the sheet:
MOUNTING HOLES
V1.00
TELAKONE OHJAIN

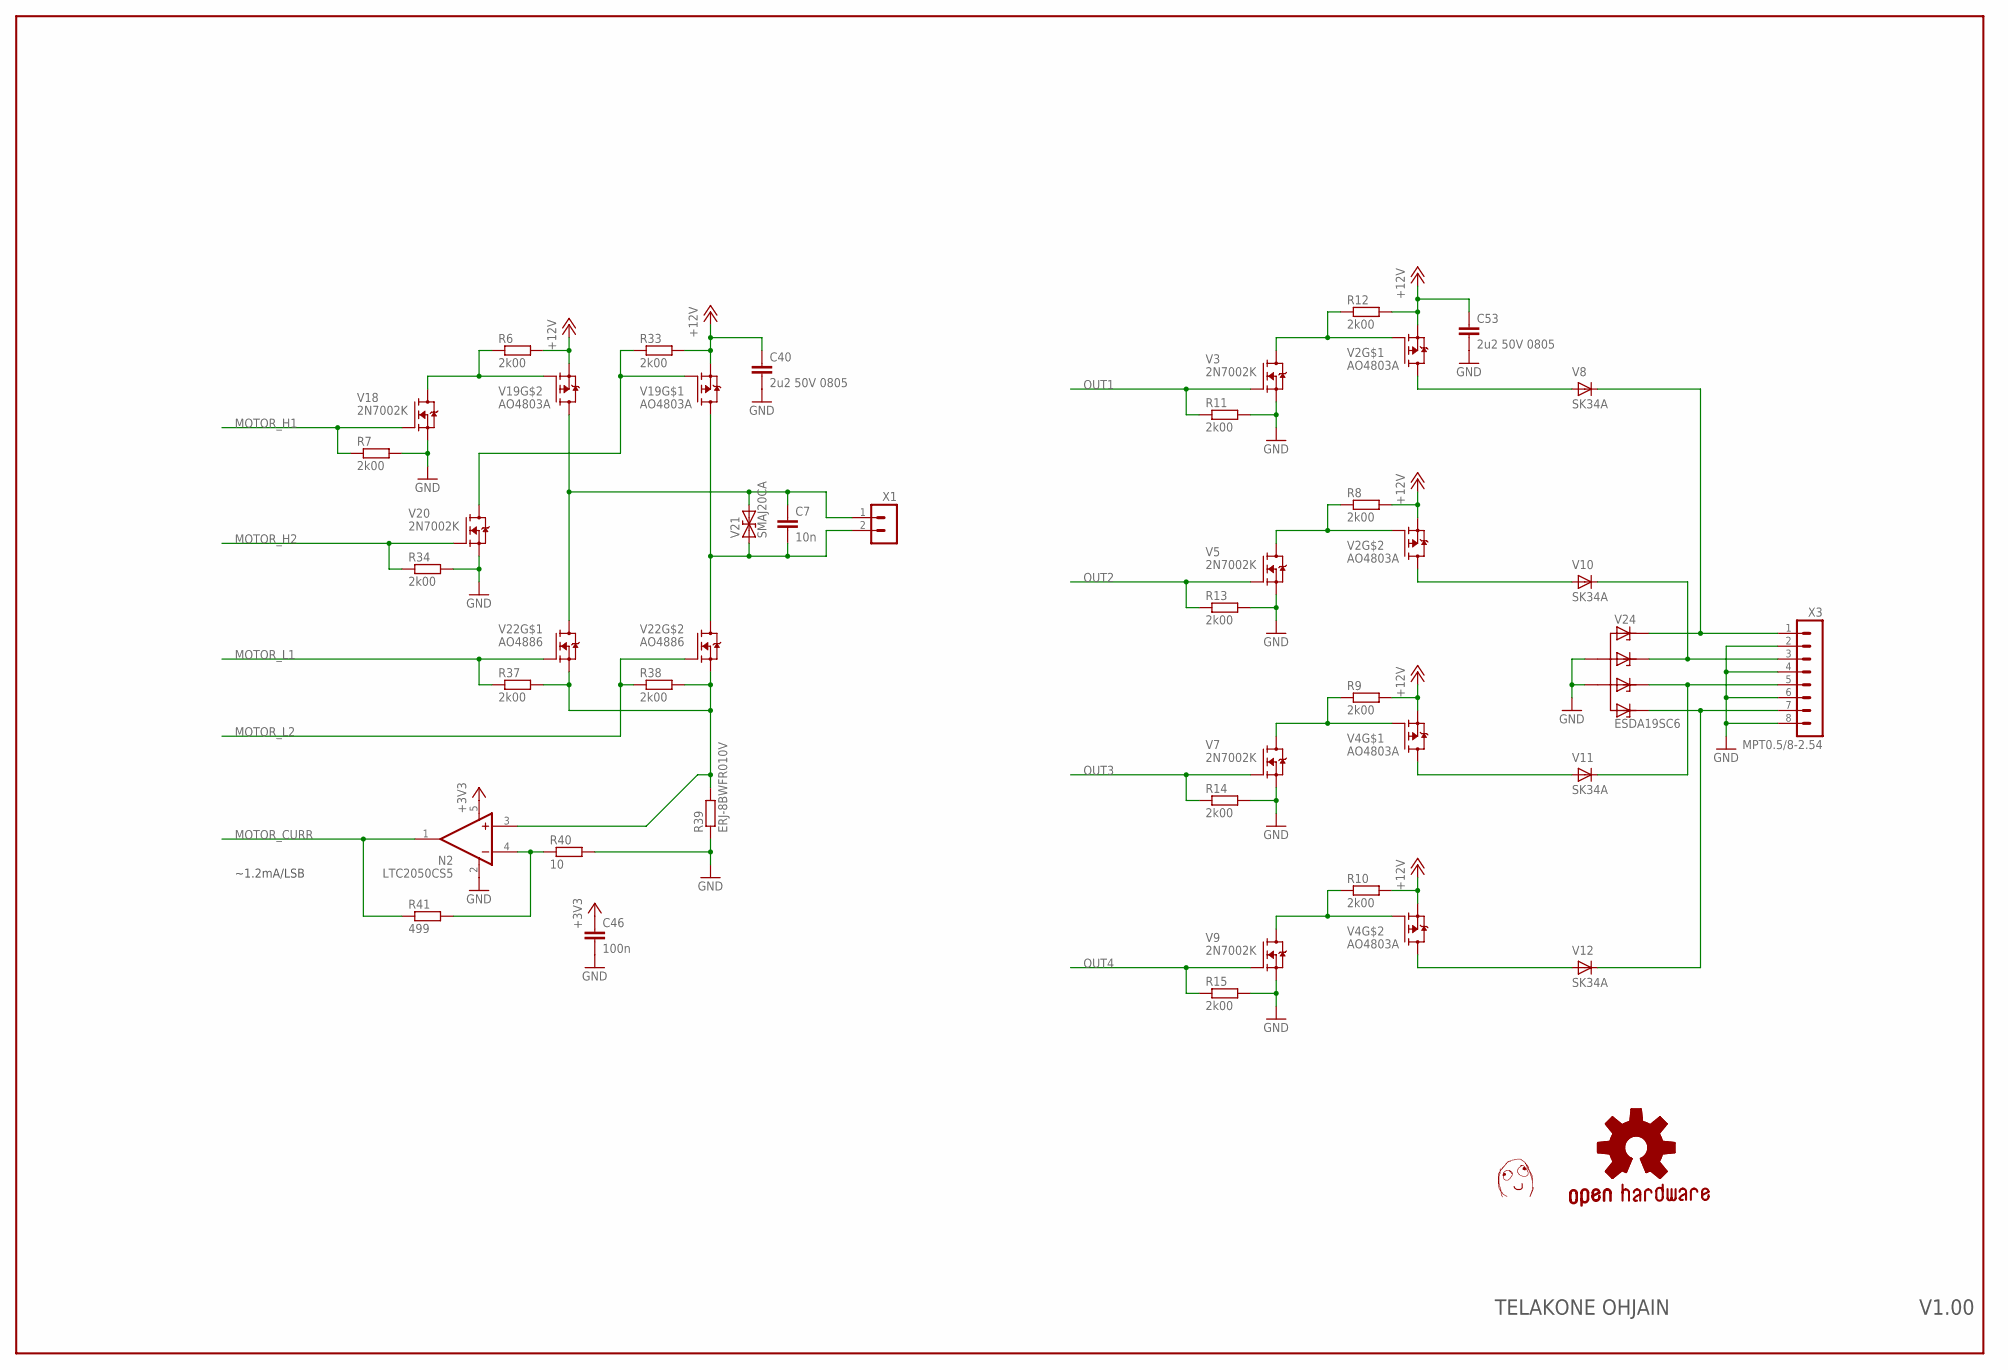
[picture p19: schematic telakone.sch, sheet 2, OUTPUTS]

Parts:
C7: 10n; C0603
C40, C53: 2u2 50V 0805; C0805
C46: 100n; C0603
N2: LTC2050CS5; SOT95P280X145-5N
R6, R7, R8, R9, R10, R11, R12, R13, R14, R15, R33, R34, R37, R38: 2k00; R0603
R39: ERJ-8BWFR010V; R1206
R40: 10; R0603
R41: 499; R0603
U$3: DAFUG
V2, V4, V19: AO4803A; SOIC8-N_MC
V3, V5, V7, V9, V18, V20: 2N7002K; SOT23
V8, V10, V11, V12: SK34A; DO214AC
V21: SMAJ20CA; DO214AC
V22: AO4886; SOIC8-N_MC
V24: ESDA19SC6; SOT23-6
X1: TE_RUUVILIITIN2
X3: MPT0.5/8-2.54

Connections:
+3V3: C46.1, N2.5 (V+); also elsewhere on the board
+12V: C40.1, C53.1, R6.2, R8.2, R9.2, R10.2, R12.2, R33.2, V2.1 (S), V2.3 (S), V4.1 (S), V4.3 (S), V19.1 (S), V19.3 (S); also elsewhere on the board
GND: C40.2, C46.2, C53.2, N2.2 (V-), R7.2, R11.2, R13.2, R14.2, R15.2, R34.2, R39.1, R40.2, V3.2 (S), V5.2 (S), V7.2 (S), V9.2 (S), V18.2 (S), V20.2 (S), V24.2 (A), V24.5 (A1), X3.2, X3.4, X3.6, X3.8; also elsewhere on the board
MOTOR_CURR: N2.1 (OUT), R41.1; also elsewhere on the board
MOTOR_H1: R7.1, V18.1 (G); also elsewhere on the board
MOTOR_H2: R34.1, V20.1 (G); also elsewhere on the board
MOTOR_L1: R37.1, V22.4 (G); also elsewhere on the board
MOTOR_L2: R38.1, V22.2 (G); also elsewhere on the board
unnamed: R6.1, V18.3 (D), V19.2 (G)
unnamed: R33.1, V19.4 (G), V20.3 (D)
unnamed: N2.3 (+IN), R37.2, R38.2, R39.2, V22.1 (S), V22.3 (S)
unnamed: N2.4 (-IN), R40.1, R41.2
unnamed: R8.1, V2.2 (G), V5.3 (D)
unnamed: R12.1, V2.4 (G), V3.3 (D)
unnamed: R9.1, V4.4 (G), V7.3 (D)
unnamed: R10.1, V4.2 (G), V9.3 (D)
unnamed: V12.C, V24.6 (C3), X3.7
unnamed: V11.C, V24.4 (C2), X3.5
unnamed: V10.C, V24.3 (C1), X3.3
unnamed: V8.C, V24.1 (C), X3.1
NERT: V2.5 (D), V2.6 (D), V8.A
NERT1: V2.7 (D), V2.8 (D), V10.A
NERT2: V4.5 (D), V4.6 (D), V11.A
NERT3: V4.7 (D), V4.8 (D), V12.A
NERT4: C7.1, V19.7 (D), V19.8 (D), V21.A (2), V22.5 (D), V22.6 (D), X1.1
NERT5: C7.2, V19.5 (D), V19.6 (D), V21.C (1), V22.7 (D), V22.8 (D), X1.2
OUT1: R11.1, V3.1 (G); also elsewhere on the board
OUT2: R13.1, V5.1 (G); also elsewhere on the board
OUT3: R14.1, V7.1 (G); also elsewhere on the board
OUT4: R15.1, V9.1 (G); also elsewhere on the board

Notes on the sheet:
~1.2mA/LSB
V1.00
TELAKONE OHJAIN

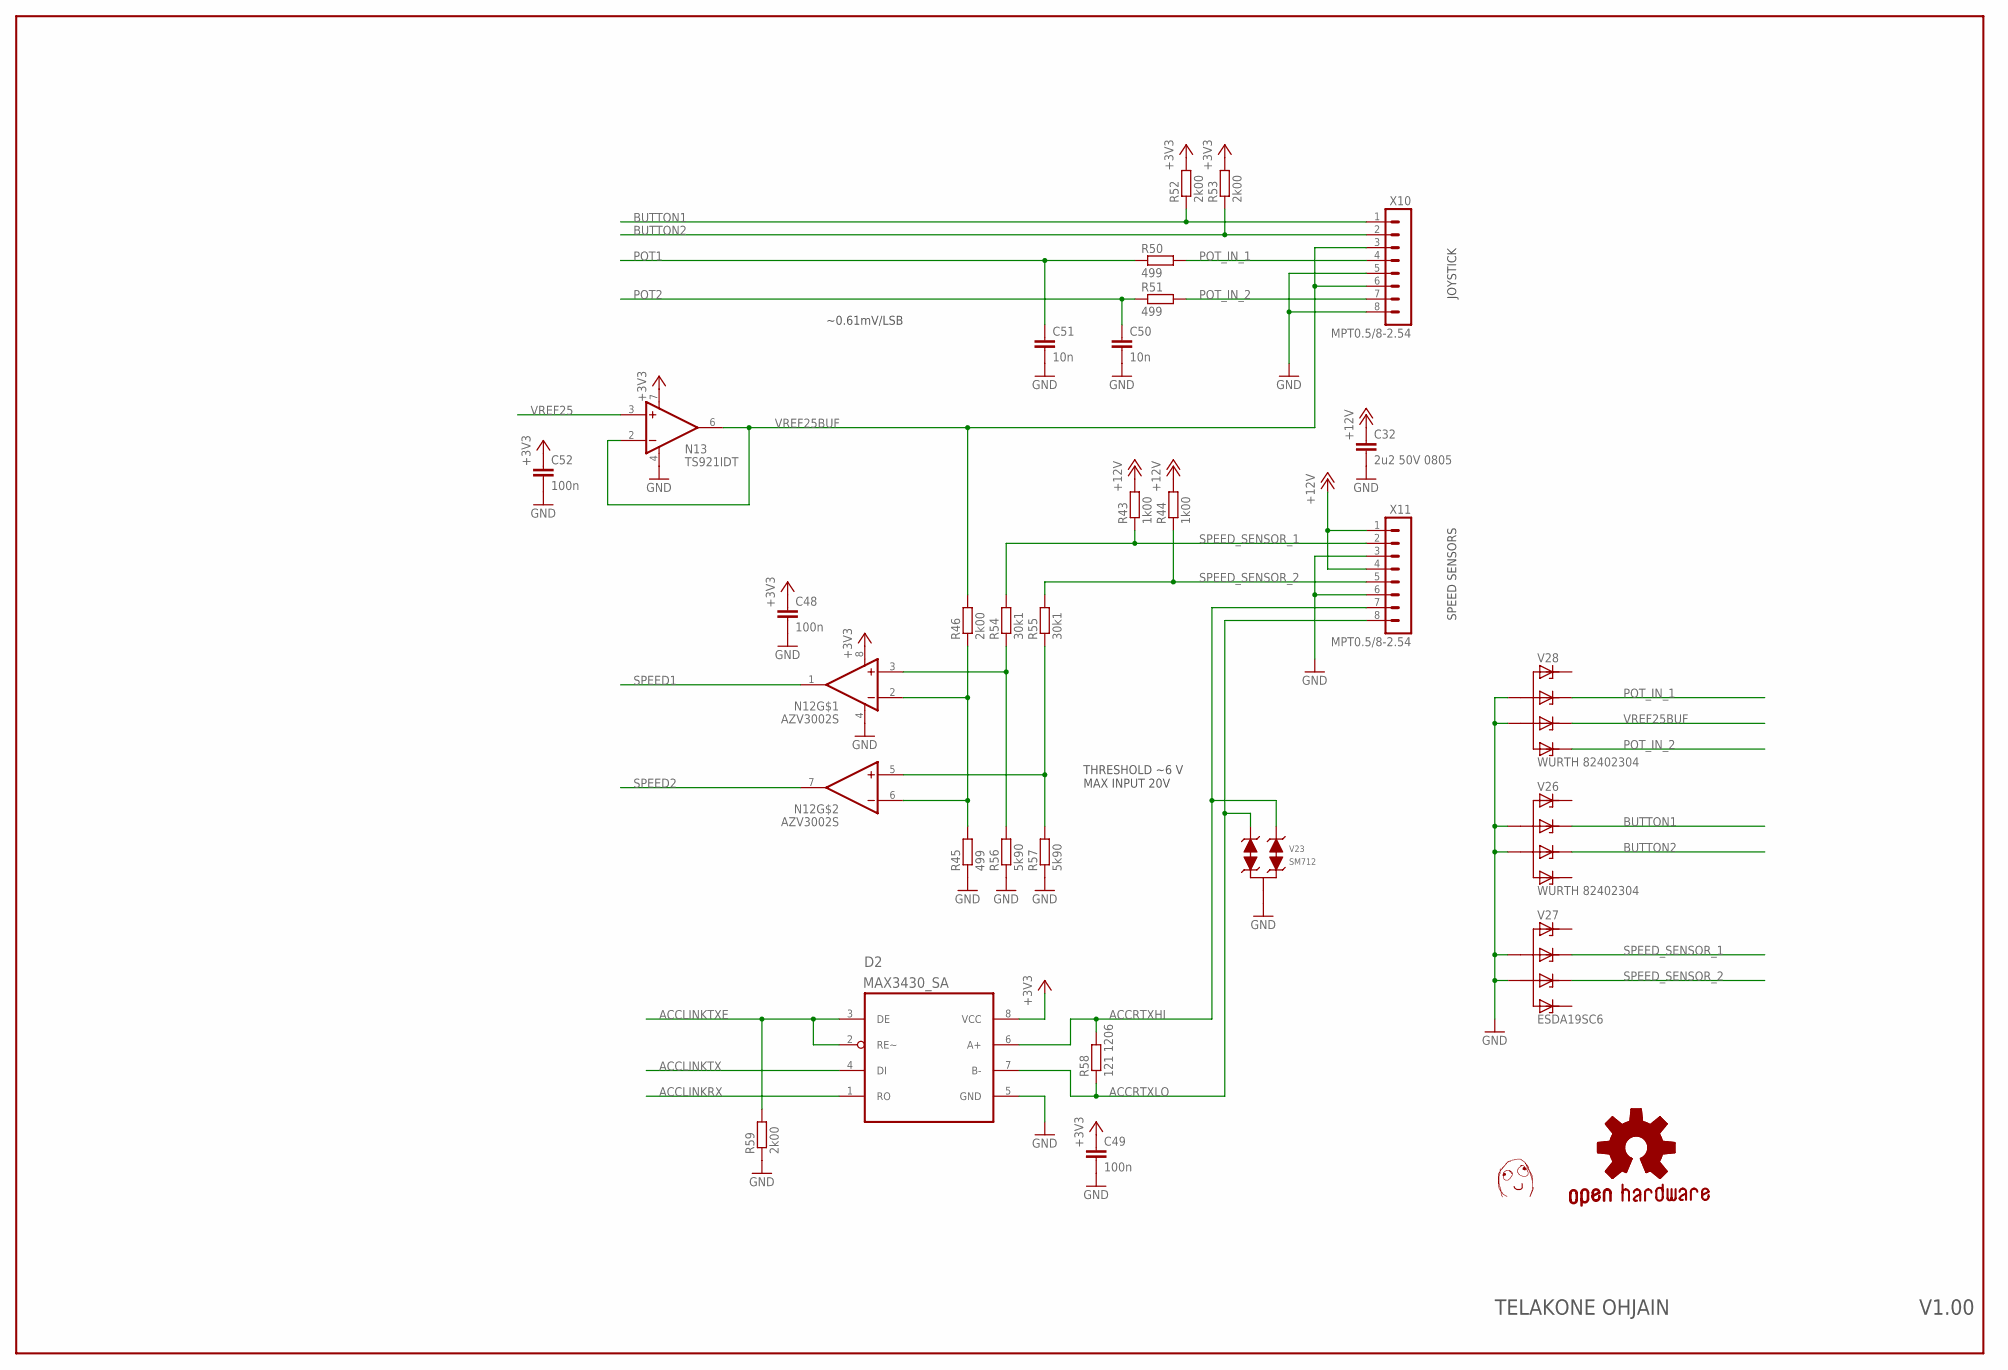
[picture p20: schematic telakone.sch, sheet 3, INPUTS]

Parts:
C32: 2u2 50V 0805; C0805
C48, C49, C52: 100n; C0603
C50, C51: 10n; C0603
D2: MAX3430_SA; SOIC8-N_MC
N12: AZV3002S; SOIC8-N_MC
N13: TS921IDT; SOIC8-N_MC
R43, R44: 1k00; R0603
R45, R50, R51: 499; R0603
R46, R52, R53, R59: 2k00; R0603
R54, R55: 30k1; R0603
R56, R57: 5k90; R0603
R58: 121 1206; R1206
U$5: DAFUG
V23: SM712; SOT23
V26, V28: WURTH 82402304; SOT23-6
V27: ESDA19SC6; SOT23-6
X10, X11: MPT0.5/8-2.54

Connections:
+3V3: C48.1, C49.1, C52.1, D2.8 (VCC), N12.8 (V+), N13.7 (V+), R52.2, R53.2; also elsewhere on the board
+12V: C32.1, R43.2, R44.2, X11.1, X11.4; also elsewhere on the board
ACCLINKRX: D2.1 (RO); also elsewhere on the board
ACCLINKTX: D2.4 (DI); also elsewhere on the board
ACCLINKTXE: D2.2 (RE~), D2.3 (DE), R59.2; also elsewhere on the board
ACCRTXHI: D2.6 (A+), R58.2, V23.1, X11.7
ACCRTXLO: D2.7 (B-), R58.1, V23.2, X11.8
BUTTON1: R52.1, V26.3 (C1), X10.1; also elsewhere on the board
BUTTON2: R53.1, V26.4 (C2), X10.2; also elsewhere on the board
GND: C32.2, C48.2, C49.2, C50.2, C51.2, C52.2, D2.5 (GND), N12.4 (V-), N13.4 (V-), R45.1, R56.1, R57.1, R59.1, V23.3, V26.2 (A), V26.5 (A1), V27.2 (A), V27.5 (A1), V28.2 (A), V28.5 (A1), X10.5, X10.8, X11.3, X11.6; also elsewhere on the board
unnamed: N12.3 (+IN), R54.1, R56.2
unnamed: N12.5 (+IN), R55.1, R57.2
unnamed: N12.2 (-IN), N12.6 (-IN), R45.2, R46.1
POT1: C51.1, R50.1; also elsewhere on the board
POT2: C50.1, R51.1; also elsewhere on the board
POT_IN_1: R50.2, V28.3 (C1), X10.4
POT_IN_2: R51.2, V28.6 (C3), X10.7
SPEED1: N12.1 (OUT); also elsewhere on the board
SPEED2: N12.7 (OUT); also elsewhere on the board
SPEED_SENSOR_1: R43.1, R54.2, V27.3 (C1), X11.2
SPEED_SENSOR_2: R44.1, R55.2, V27.4 (C2), X11.5
VREF25: N13.3 (+IN); also elsewhere on the board
VREF25BUF: N13.2 (-IN), N13.6 (OUT), R46.2, V28.4 (C2), X10.3, X10.6

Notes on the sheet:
JOYSTICK
~0.61mV/LSB
THRESHOLD ~6 V MAX INPUT 20V
SPEED SENSORS
V1.00
TELAKONE OHJAIN

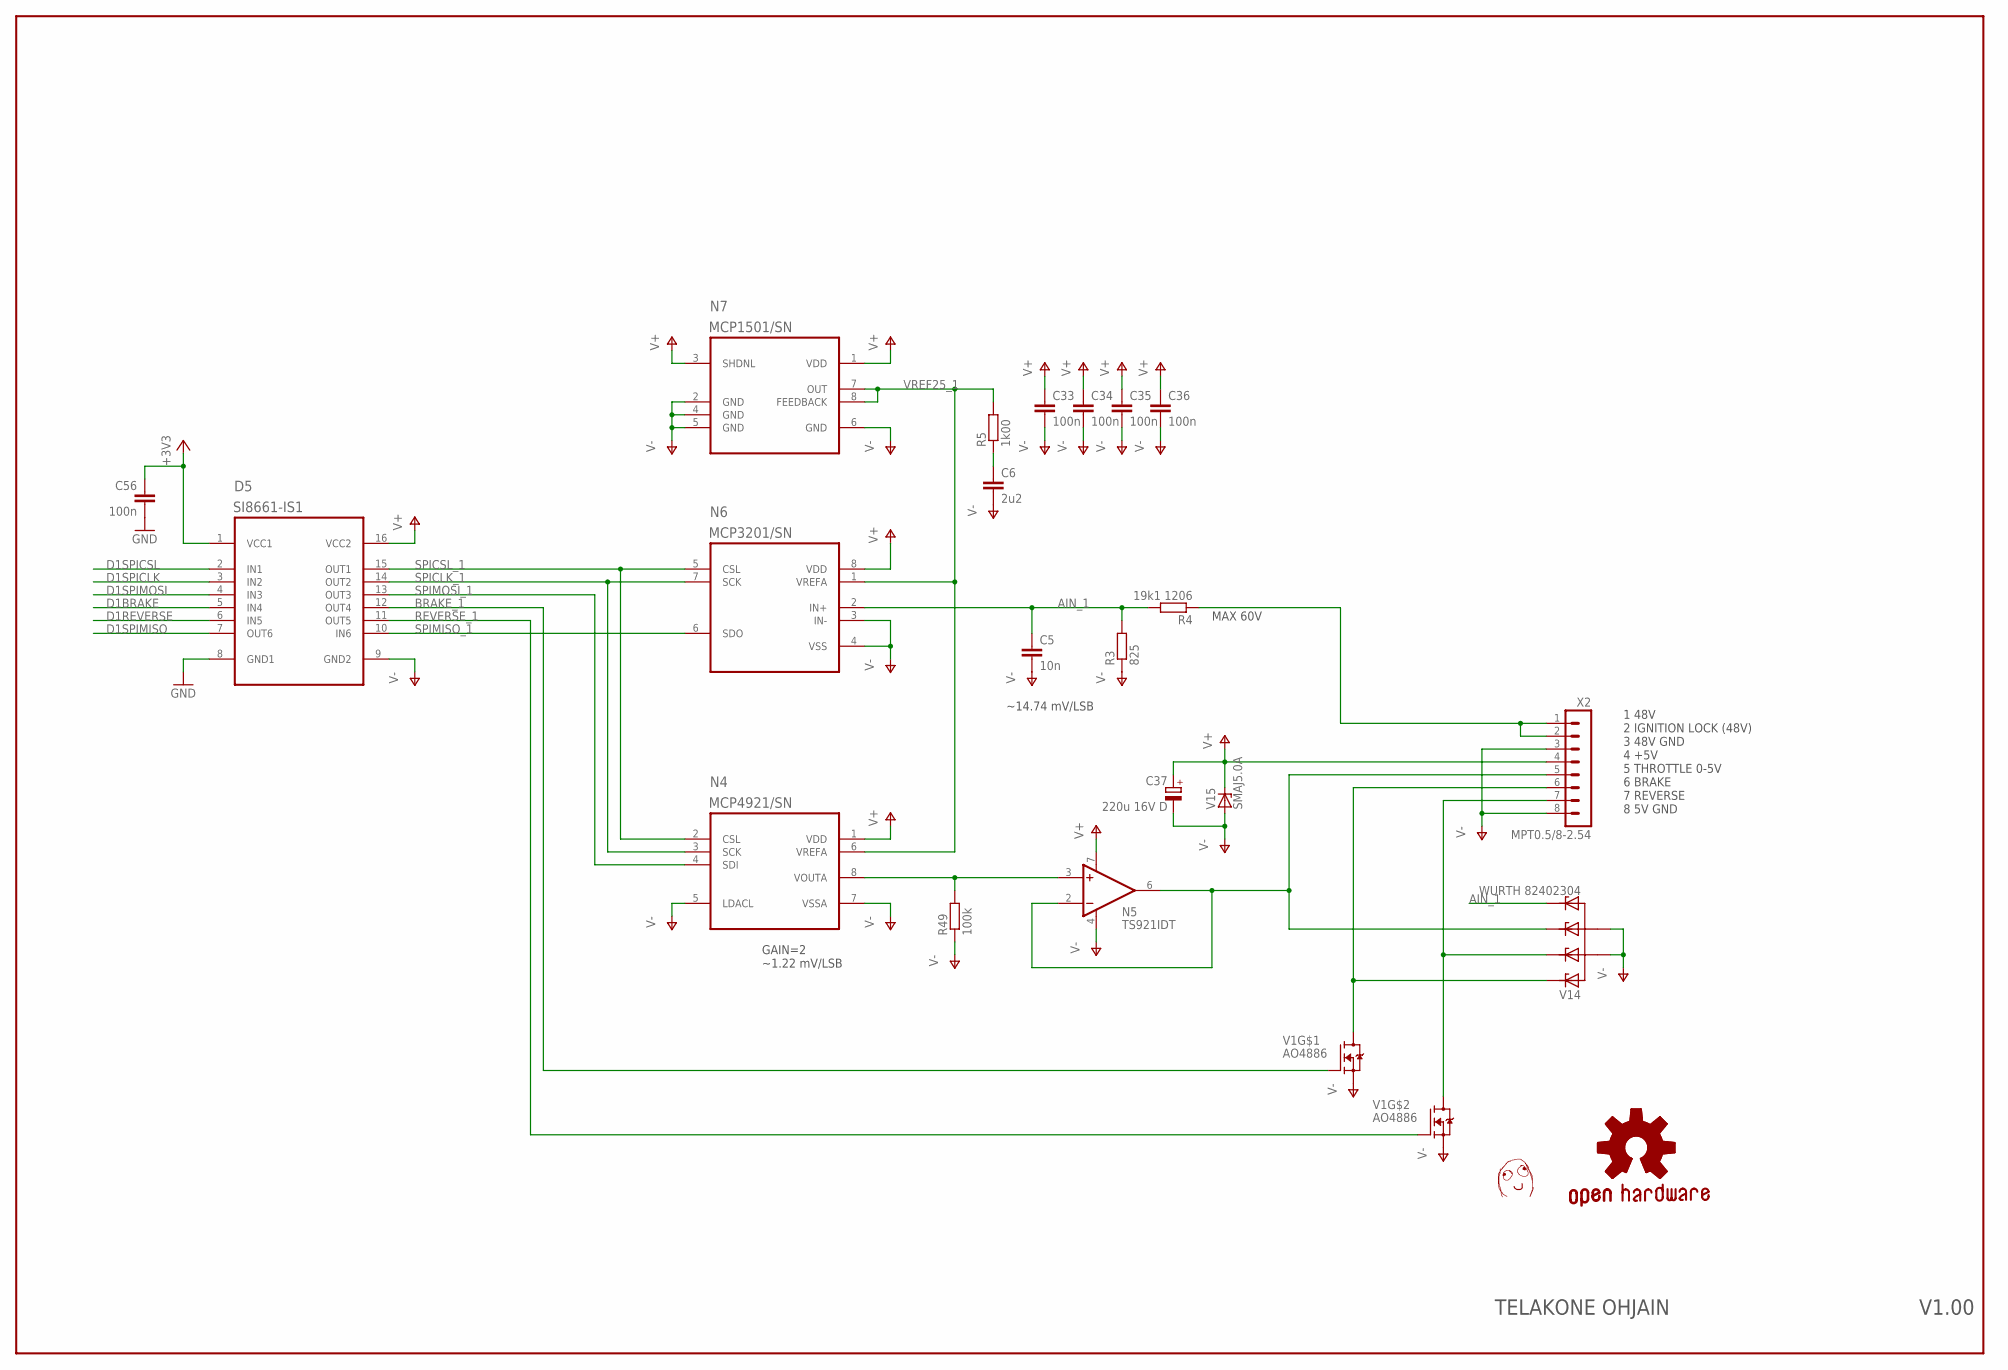
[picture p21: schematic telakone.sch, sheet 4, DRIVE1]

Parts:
C5: 10n; C0603
C6: 2u2; C0603
C33, C34, C35, C36, C56: 100n; C0603
C37: 220u 16V D; CT7343
D5: SI8661-IS1; SOIC16-N
N4: MCP4921/SN; SOIC8-N_MC
N5: TS921IDT; SOIC8-N_MC
N6: MCP3201/SN; SOIC8-N_MC
N7: MCP1501/SN; SOIC8-N_MC
R3: 825; R0603
R4: 19k1 1206; R1206
R5: 1k00; R0603
R49: 100k; R0603
U$7: DAFUG
V1: AO4886; SOIC8-N_MC
V14: WURTH 82402304; SOT23-6
V15: SMAJ5.0A; DO214AC
X2: MPT0.5/8-2.54

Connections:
+3V3: C56.1, D5.1 (VCC1); also elsewhere on the board
+48V_1: R4.1, X2.1, X2.2
AIN_1: C5.1, N6.2 (IN+), R3.2, R4.2, V14.6 (C3)
BRAKE_1: D5.12 (OUT4), V1.4 (G)
BRAKE_OD_1: V1.5 (D), V1.6 (D), V14.1 (C), X2.6
D1BRAKE: D5.5 (IN4); also elsewhere on the board
D1REVERSE: D5.6 (IN5); also elsewhere on the board
D1SPICLK: D5.3 (IN2); also elsewhere on the board
D1SPICSL: D5.2 (IN1); also elsewhere on the board
D1SPIMISO: D5.7 (OUT6); also elsewhere on the board
D1SPIMOSI: D5.4 (IN3); also elsewhere on the board
GND: C56.2, D5.8 (GND1); also elsewhere on the board
unnamed: C6.1, R5.1
REVERSE_1: D5.11 (OUT5), V1.2 (G)
REVERSE_OD_1: V1.7 (D), V1.8 (D), V14.3 (C1), X2.7
SPICLK_1: D5.14 (OUT2), N4.3 (SCK), N6.7 (SCK)
SPICSL_1: D5.15 (OUT1), N4.2 (CSL), N6.5 (CSL)
SPIMISO_1: D5.10 (IN6), N6.6 (SDO)
SPIMOSI_1: D5.13 (OUT3), N4.4 (SDI)
THROTTLE_1: N4.8 (VOUTA), N5.3 (+IN), R49.2
THROTTLE_BUFFERED_1: N5.2 (-IN), N5.6 (OUT), V14.4 (C2), X2.5
V+1: C33.1, C34.1, C35.1, C36.1, C37.+, D5.16 (VCC2), N4.1 (VDD), N5.7 (V+), N6.8 (VDD), N7.1 (VDD), N7.3 (SHDNL), V15.C, X2.4
V-1: C5.2, C6.2, C33.2, C34.2, C35.2, C36.2, C37.-, D5.9 (GND2), N4.5 (LDACL), N4.7 (VSSA), N5.4 (V-), N6.3 (IN-), N6.4 (VSS), N7.2 (GND), N7.4 (GND), N7.5 (GND), N7.6 (GND), R3.1, R49.1, V1.1 (S), V1.3 (S), V14.2 (A), V14.5 (A1), V15.A, X2.3, X2.8
VREF25_1: N4.6 (VREFA), N6.1 (VREFA), N7.7 (OUT), N7.8 (FEEDBACK), R5.2

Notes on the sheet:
1 48V 2 IGNITION LOCK (48V) 3 48V GND 4 +5V 5 THROTTLE 0-5V 6 BRAKE 7 REVERSE 8 5V GND
MAX 60V
~14.74 mV/LSB
GAIN=2 ~1.22 mV/LSB
V1.00
TELAKONE OHJAIN

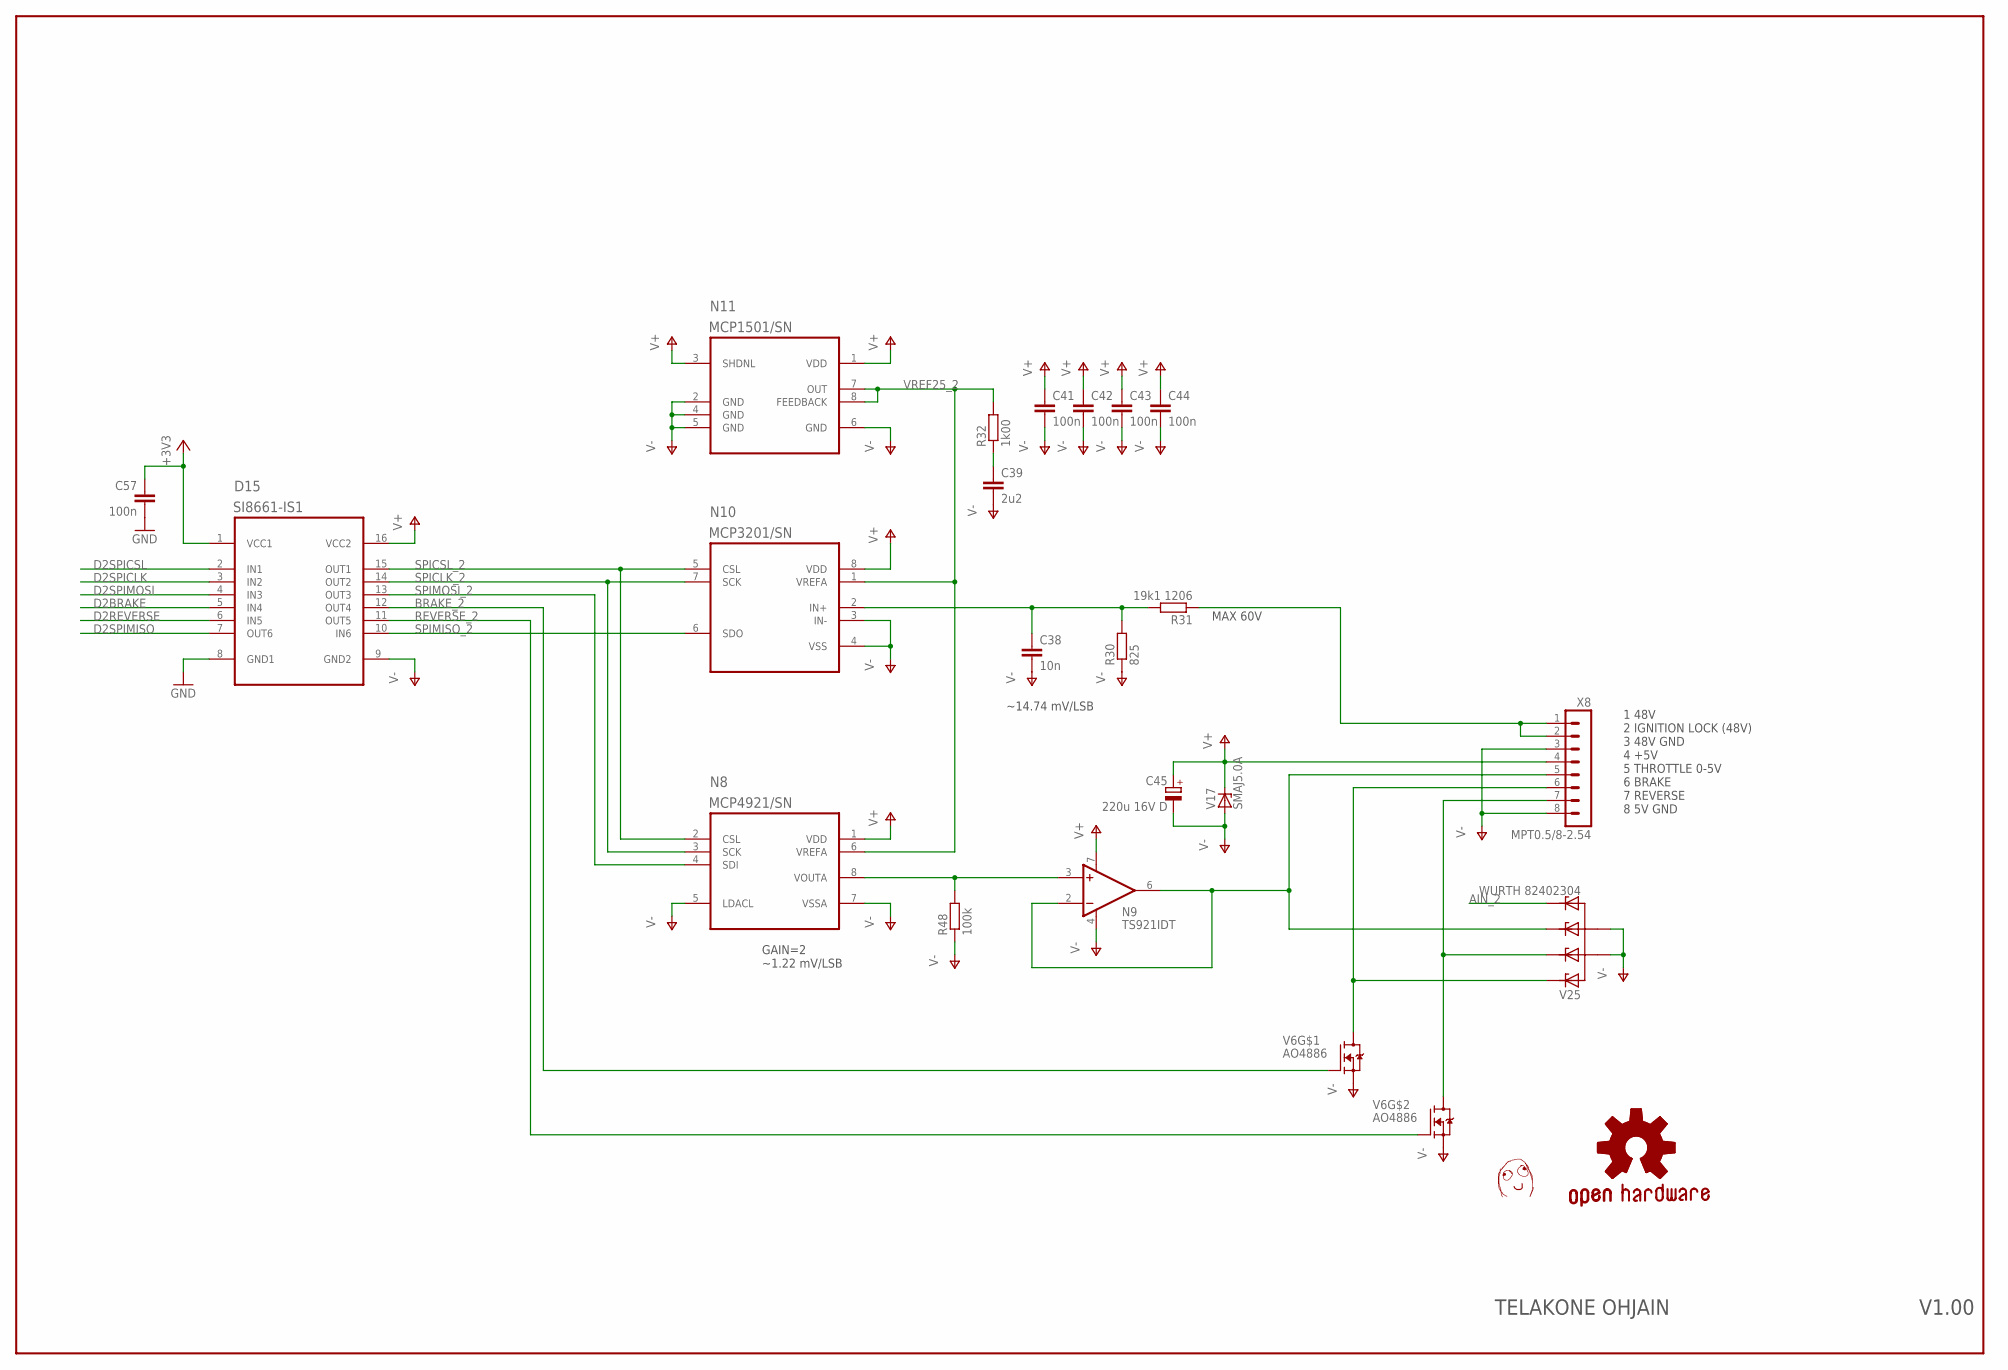
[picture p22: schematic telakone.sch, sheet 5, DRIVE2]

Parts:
C38: 10n; C0603
C39: 2u2; C0603
C41, C42, C43, C44, C57: 100n; C0603
C45: 220u 16V D; CT7343
D15: SI8661-IS1; SOIC16-N
N8: MCP4921/SN; SOIC8-N_MC
N9: TS921IDT; SOIC8-N_MC
N10: MCP3201/SN; SOIC8-N_MC
N11: MCP1501/SN; SOIC8-N_MC
R30: 825; R0603
R31: 19k1 1206; R1206
R32: 1k00; R0603
R48: 100k; R0603
U$9: DAFUG
V6: AO4886; SOIC8-N_MC
V17: SMAJ5.0A; DO214AC
V25: WURTH 82402304; SOT23-6
X8: MPT0.5/8-2.54

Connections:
+3V3: C57.1, D15.1 (VCC1); also elsewhere on the board
+48V_2: R31.1, X8.1, X8.2
AIN_2: C38.1, N10.2 (IN+), R30.2, R31.2, V25.6 (C3)
BRAKE_2: D15.12 (OUT4), V6.4 (G)
BRAKE_OD_2: V6.5 (D), V6.6 (D), V25.1 (C), X8.6
D2BRAKE: D15.5 (IN4); also elsewhere on the board
D2REVERSE: D15.6 (IN5); also elsewhere on the board
D2SPICLK: D15.3 (IN2); also elsewhere on the board
D2SPICSL: D15.2 (IN1); also elsewhere on the board
D2SPIMISO: D15.7 (OUT6); also elsewhere on the board
D2SPIMOSI: D15.4 (IN3); also elsewhere on the board
GND: C57.2, D15.8 (GND1); also elsewhere on the board
unnamed: C39.1, R32.1
REVERSE_2: D15.11 (OUT5), V6.2 (G)
REVERSE_OD_2: V6.7 (D), V6.8 (D), V25.3 (C1), X8.7
SPICLK_2: D15.14 (OUT2), N8.3 (SCK), N10.7 (SCK)
SPICSL_2: D15.15 (OUT1), N8.2 (CSL), N10.5 (CSL)
SPIMISO_2: D15.10 (IN6), N10.6 (SDO)
SPIMOSI_2: D15.13 (OUT3), N8.4 (SDI)
THROTTLE_2: N8.8 (VOUTA), N9.3 (+IN), R48.2
THROTTLE_BUFFERED_2: N9.2 (-IN), N9.6 (OUT), V25.4 (C2), X8.5
V+2: C41.1, C42.1, C43.1, C44.1, C45.+, D15.16 (VCC2), N8.1 (VDD), N9.7 (V+), N10.8 (VDD), N11.1 (VDD), N11.3 (SHDNL), V17.C, X8.4
V-2: C38.2, C39.2, C41.2, C42.2, C43.2, C44.2, C45.-, D15.9 (GND2), N8.5 (LDACL), N8.7 (VSSA), N9.4 (V-), N10.3 (IN-), N10.4 (VSS), N11.2 (GND), N11.4 (GND), N11.5 (GND), N11.6 (GND), R30.1, R48.1, V6.1 (S), V6.3 (S), V17.A, V25.2 (A), V25.5 (A1), X8.3, X8.8
VREF25_2: N8.6 (VREFA), N10.1 (VREFA), N11.7 (OUT), N11.8 (FEEDBACK), R32.2

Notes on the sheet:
1 48V 2 IGNITION LOCK (48V) 3 48V GND 4 +5V 5 THROTTLE 0-5V 6 BRAKE 7 REVERSE 8 5V GND
MAX 60V
~14.74 mV/LSB
GAIN=2 ~1.22 mV/LSB
V1.00
TELAKONE OHJAIN

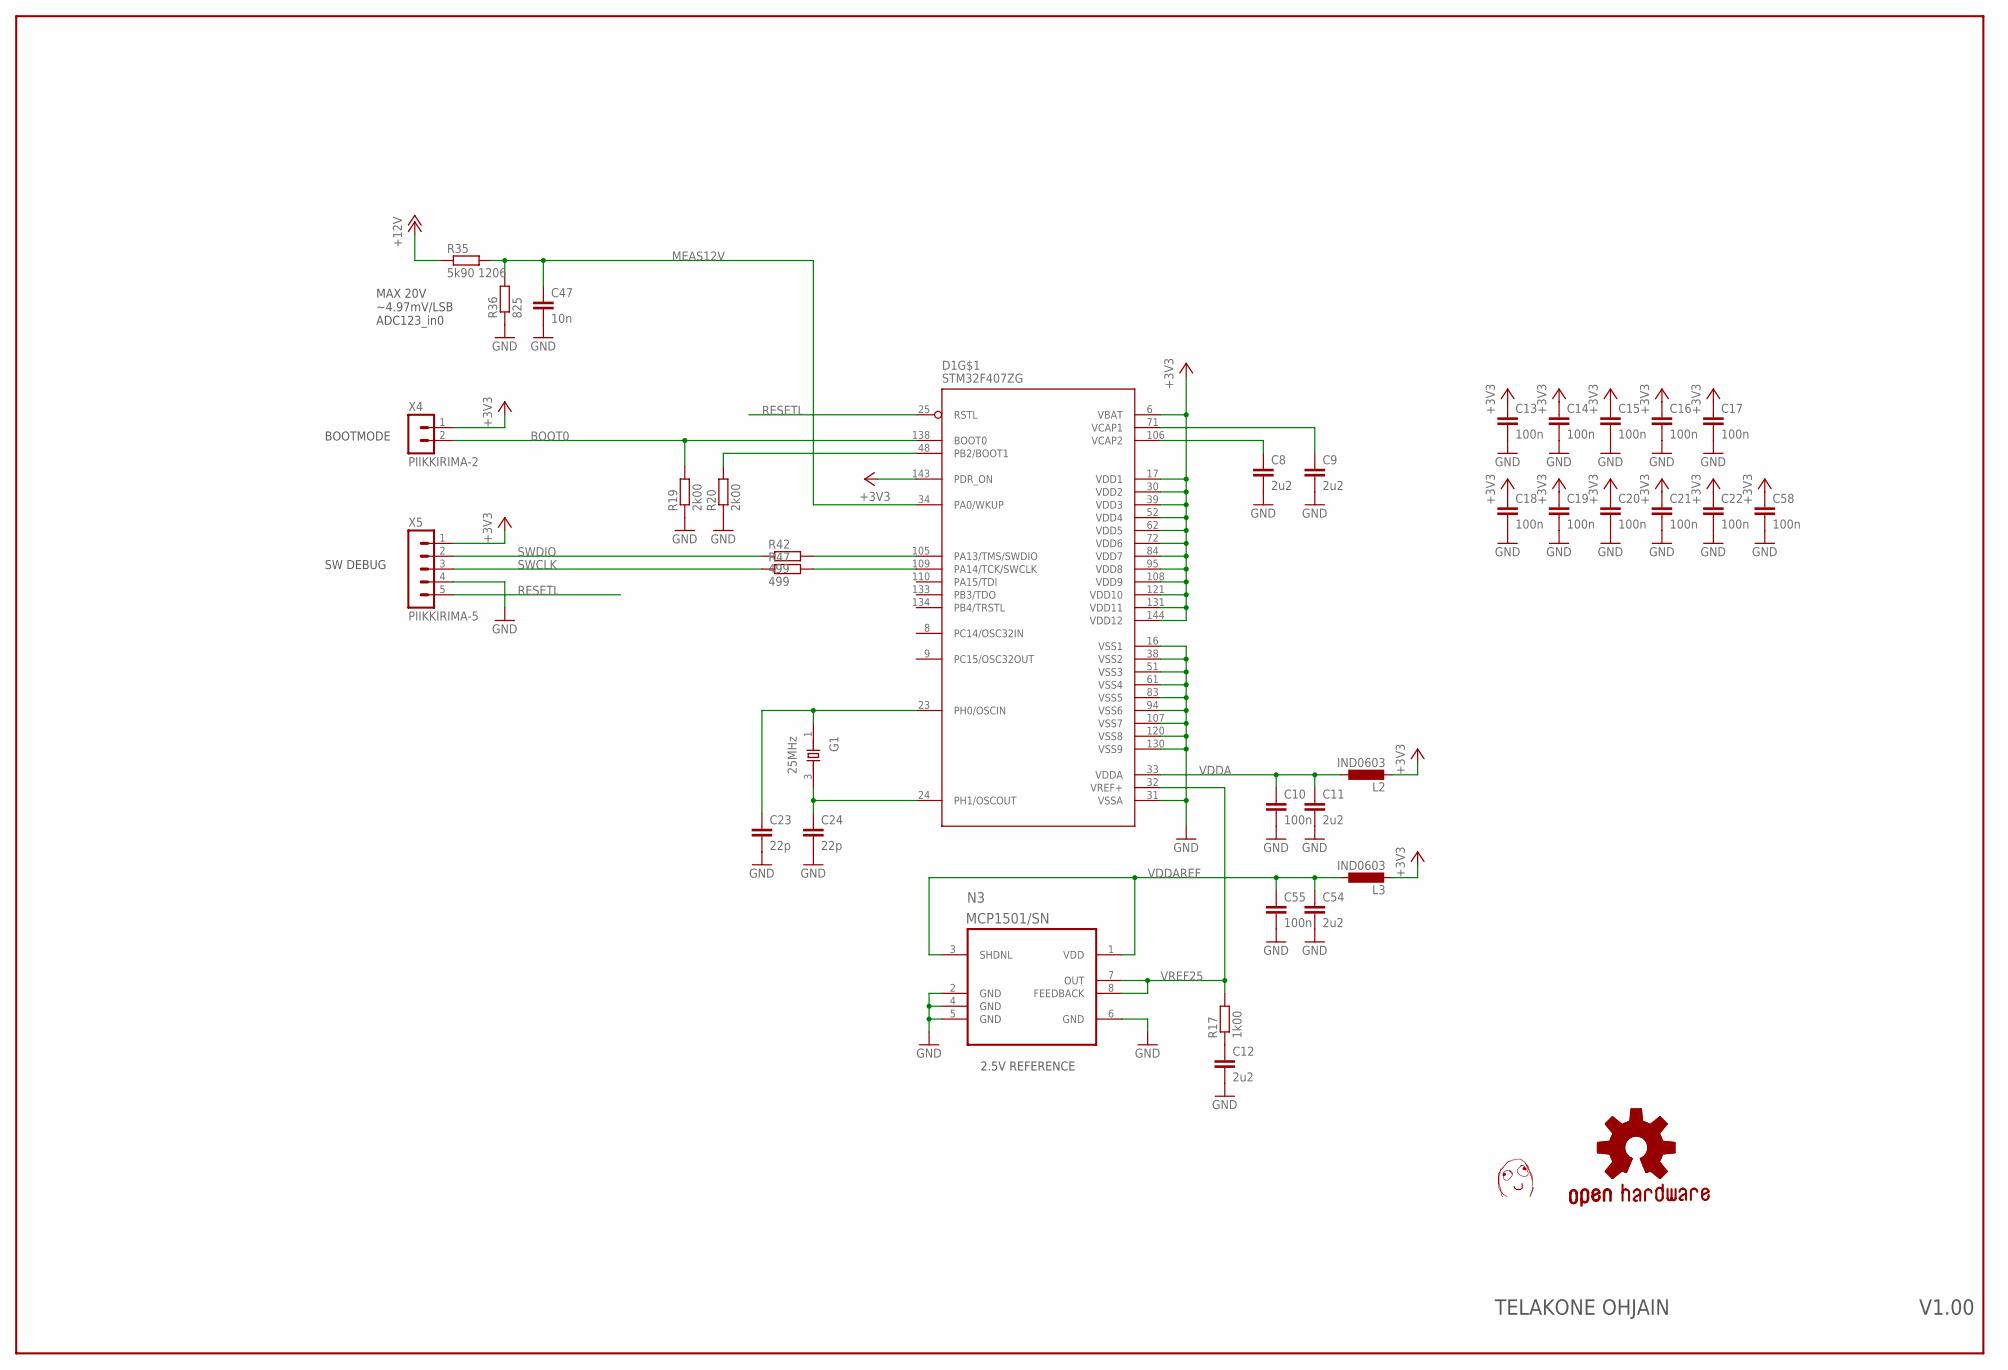
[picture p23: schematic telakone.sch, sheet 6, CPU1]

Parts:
C8, C9, C11, C12, C54: 2u2; C0603
C10, C13, C14, C15, C16, C17, C18, C19, C20, C21, C22, C55, C58: 100n; C0603
C23, C24: 22p; C0603
C47: 10n; C0603
D1: STM32F407ZG; LQFP-144
G1: 25MHz; X_3225
L2, L3: IND0603; R0603
N3: MCP1501/SN; SOIC8-N_MC
R17: 1k00; R0603
R19, R20: 2k00; R0603
R35: 5k90 1206; R1206
R36: 825; R0603
R42, R47: 499; R0603
U$11: DAFUG
X4: PIIKKIRIMA-2
X5: PIIKKIRIMA-5

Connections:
+3V3: C13.1, C14.1, C15.1, C16.1, C17.1, C18.1, C19.1, C20.1, C21.1, C22.1, C58.1, D1.6 (VBAT), D1.17 (VDD1), D1.30 (VDD2), D1.39 (VDD3), D1.52 (VDD4), D1.62 (VDD5), D1.72 (VDD6), D1.84 (VDD7), D1.95 (VDD8), D1.108 (VDD9), D1.121 (VDD10), D1.131 (VDD11), D1.143 (PDR_ON), D1.144 (VDD12), L2.2, L3.2, X4.1, X5.1; also elsewhere on the board
+12V: R35.1; also elsewhere on the board
BOOT0: D1.138 (BOOT0), R19.2, X4.2
GND: C8.2, C9.2, C10.2, C11.2, C12.2, C13.2, C14.2, C15.2, C16.2, C17.2, C18.2, C19.2, C20.2, C21.2, C22.2, C23.2, C24.2, C47.2, C54.2, C55.2, C58.2, D1.16 (VSS1), D1.31 (VSSA), D1.38 (VSS2), D1.51 (VSS3), D1.61 (VSS4), D1.83 (VSS5), D1.94 (VSS6), D1.107 (VSS7), D1.120 (VSS8), D1.130 (VSS9), N3.2 (GND), N3.4 (GND), N3.5 (GND), N3.6 (GND), R19.1, R20.1, R36.1, X5.4; also elsewhere on the board
MEAS12V: C47.1, D1.34 (PA0/WKUP), R35.2, R36.2
unnamed: D1.109 (PA14/TCK/SWCLK), R47.2
unnamed: D1.105 (PA13/TMS/SWDIO), R42.2
unnamed: C12.1, R17.1
unnamed: D1.48 (PB2/BOOT1), R20.2
OSCIN: C23.1, D1.23 (PH0/OSCIN), G1.1 (X1)
OSCOUT: C24.1, D1.24 (PH1/OSCOUT), G1.3 (X2)
RESETL: D1.25 (RSTL), X5.5; also elsewhere on the board
SWCLK: R47.1, X5.3
SWDIO: R42.1, X5.2
VCAP1: C9.1, D1.71 (VCAP1)
VCAP2: C8.1, D1.106 (VCAP2)
VDDA: C10.1, C11.1, D1.33 (VDDA), L2.1
VDDAREF: C54.1, C55.1, L3.1, N3.1 (VDD), N3.3 (SHDNL)
VREF25: D1.32 (VREF+), N3.7 (OUT), N3.8 (FEEDBACK), R17.2; also elsewhere on the board

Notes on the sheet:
2.5V REFERENCE
SW DEBUG
BOOTMODE
MAX 20V ~4.97mV/LSB ADC123_in0
V1.00
TELAKONE OHJAIN

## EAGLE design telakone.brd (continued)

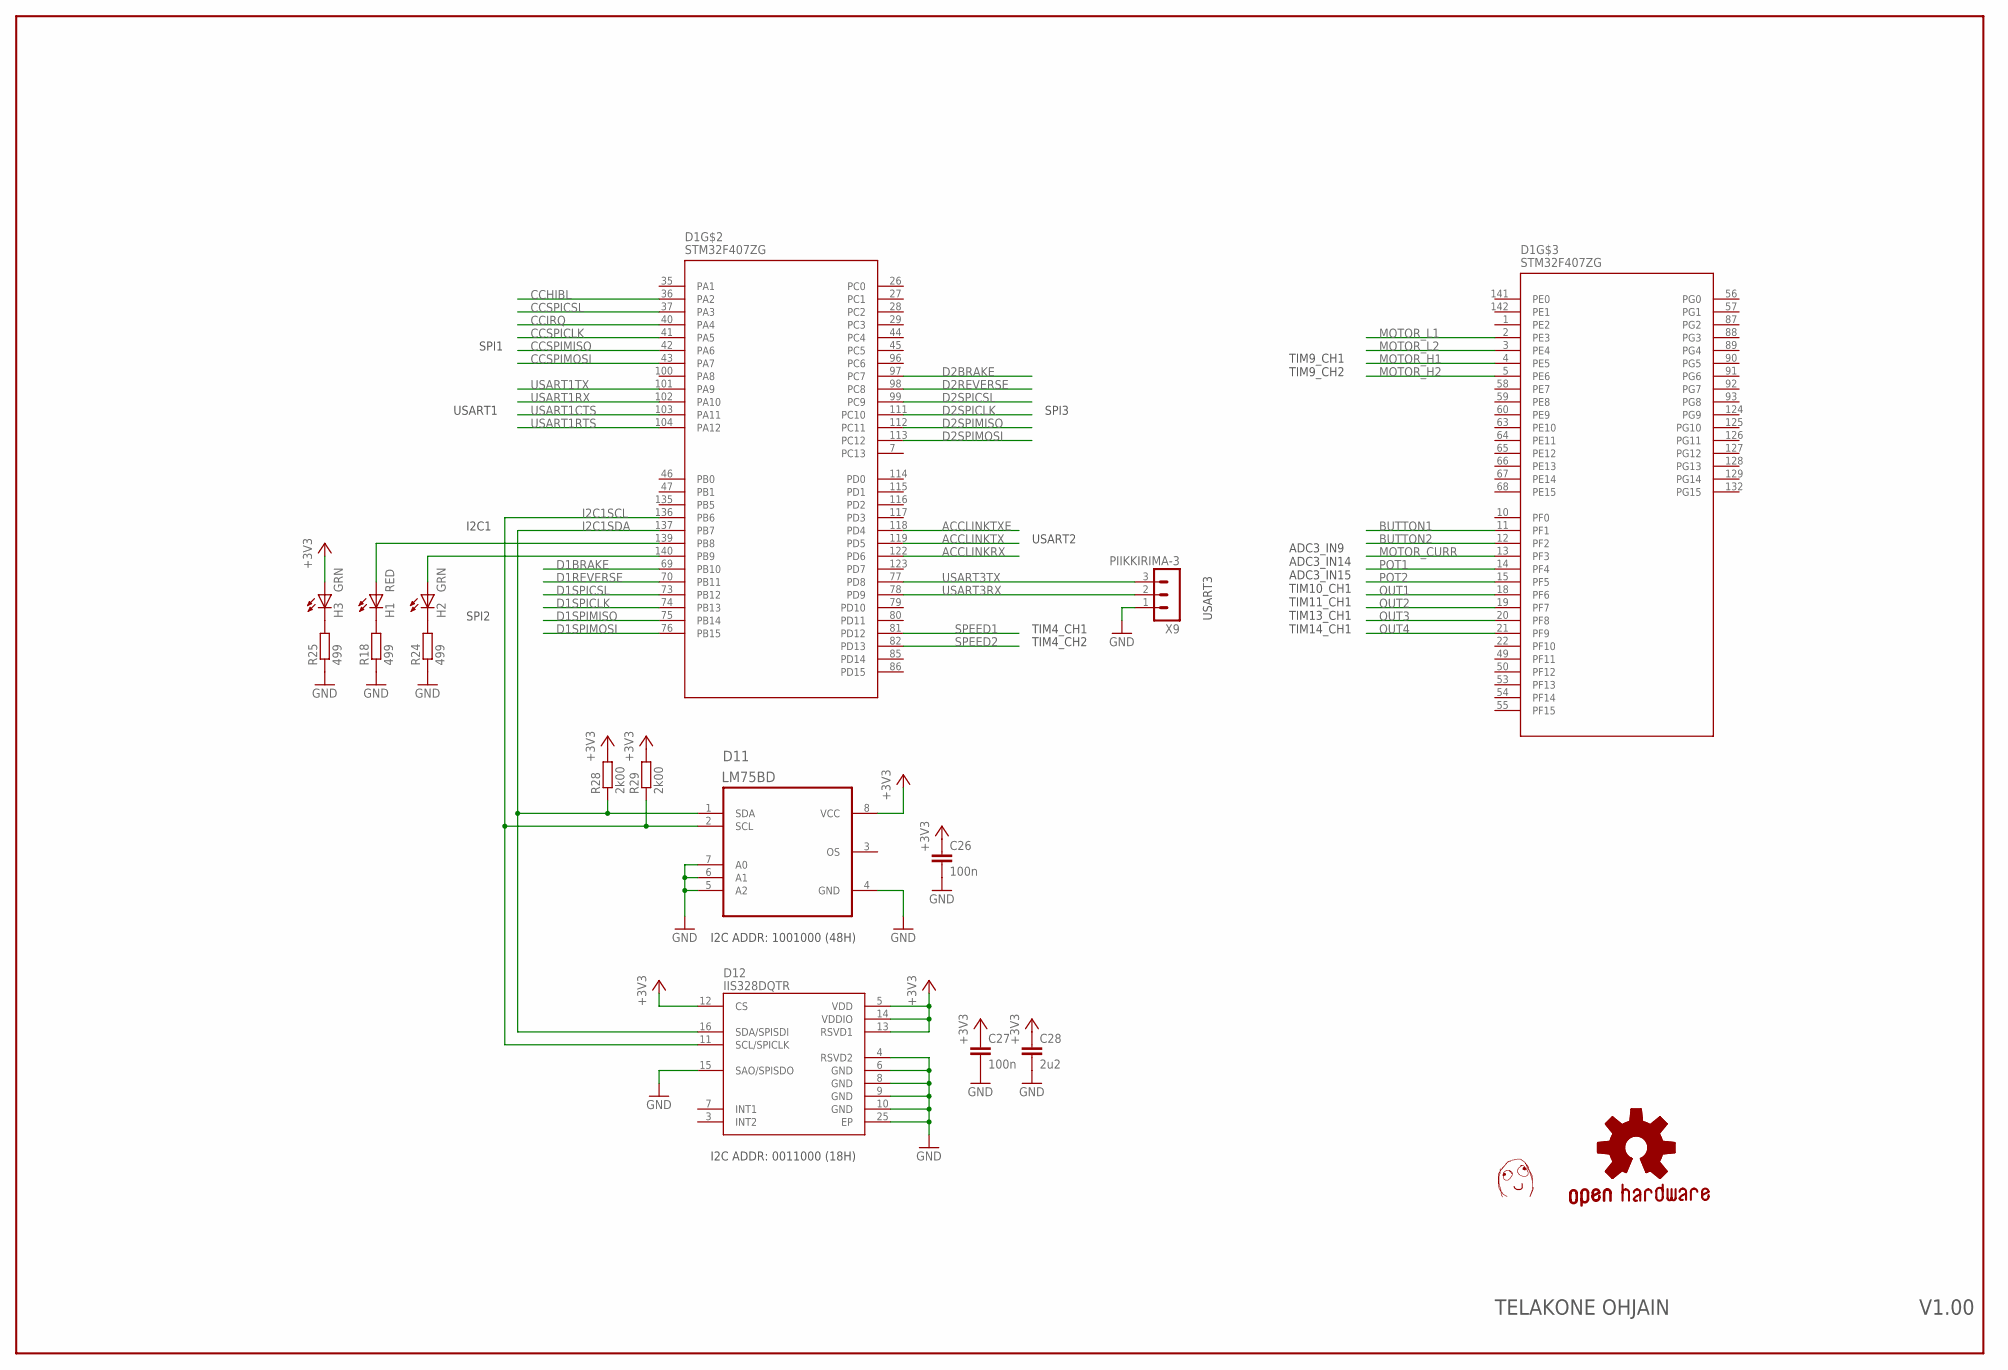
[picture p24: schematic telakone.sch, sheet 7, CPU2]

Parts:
C26, C27: 100n; C0603
C28: 2u2; C0603
D1: STM32F407ZG; LQFP-144
D11: LM75BD; SOIC8-N_MC
D12: IIS328DQTR; QFN50P400X400X100-25N
H1: RED; CHIP-LED0603
H2, H3: GRN; CHIP-LED0603
R18, R24, R25: 499; R0603
R28, R29: 2k00; R0603
U$13: DAFUG
X9: PIIKKIRIMA-3

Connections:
+3V3: C26.1, C27.1, C28.1, D11.8 (VCC), D12.5 (VDD), D12.12 (CS), D12.13 (RSVD1), D12.14 (VDDIO), H3.A, R28.2, R29.2; also elsewhere on the board
ACCLINKRX: D1.122 (PD6); also elsewhere on the board
ACCLINKTX: D1.119 (PD5); also elsewhere on the board
ACCLINKTXE: D1.118 (PD4); also elsewhere on the board
BUTTON1: D1.11 (PF1); also elsewhere on the board
BUTTON2: D1.12 (PF2); also elsewhere on the board
CCHIBL: D1.36 (PA2); also elsewhere on the board
CCIRQ: D1.40 (PA4); also elsewhere on the board
CCSPICLK: D1.41 (PA5); also elsewhere on the board
CCSPICSL: D1.37 (PA3); also elsewhere on the board
CCSPIMISO: D1.42 (PA6); also elsewhere on the board
CCSPIMOSI: D1.43 (PA7); also elsewhere on the board
D1BRAKE: D1.69 (PB10); also elsewhere on the board
D1REVERSE: D1.70 (PB11); also elsewhere on the board
D1SPICLK: D1.74 (PB13); also elsewhere on the board
D1SPICSL: D1.73 (PB12); also elsewhere on the board
D1SPIMISO: D1.75 (PB14); also elsewhere on the board
D1SPIMOSI: D1.76 (PB15); also elsewhere on the board
D2BRAKE: D1.97 (PC7); also elsewhere on the board
D2REVERSE: D1.98 (PC8); also elsewhere on the board
D2SPICLK: D1.111 (PC10); also elsewhere on the board
D2SPICSL: D1.99 (PC9); also elsewhere on the board
D2SPIMISO: D1.112 (PC11); also elsewhere on the board
D2SPIMOSI: D1.113 (PC12); also elsewhere on the board
GND: C26.2, C27.2, C28.2, D11.4 (GND), D11.5 (A2), D11.6 (A1), D11.7 (A0), D12.4 (RSVD2), D12.6 (GND), D12.8 (GND), D12.9 (GND), D12.10 (GND), D12.15 (SAO/SPISDO), D12.25 (EP), R18.1, R24.1, R25.1, X9.1; also elsewhere on the board
I2C1SCL: D1.136 (PB6), D11.2 (SCL), D12.11 (SCL/SPICLK), R29.1
I2C1SDA: D1.137 (PB7), D11.1 (SDA), D12.16 (SDA/SPISDI), R28.1
MOTOR_CURR: D1.13 (PF3); also elsewhere on the board
MOTOR_H1: D1.4 (PE5); also elsewhere on the board
MOTOR_H2: D1.5 (PE6); also elsewhere on the board
MOTOR_L1: D1.2 (PE3); also elsewhere on the board
MOTOR_L2: D1.3 (PE4); also elsewhere on the board
unnamed: H2.C, R24.2
unnamed: H1.C, R18.2
unnamed: D1.139 (PB8), H1.A
unnamed: D1.140 (PB9), H2.A
unnamed: H3.C, R25.2
OUT1: D1.18 (PF6); also elsewhere on the board
OUT2: D1.19 (PF7); also elsewhere on the board
OUT3: D1.20 (PF8); also elsewhere on the board
OUT4: D1.21 (PF9); also elsewhere on the board
POT1: D1.14 (PF4); also elsewhere on the board
POT2: D1.15 (PF5); also elsewhere on the board
SPEED1: D1.81 (PD12); also elsewhere on the board
SPEED2: D1.82 (PD13); also elsewhere on the board
USART1CTS: D1.103 (PA11); also elsewhere on the board
USART1RTS: D1.104 (PA12); also elsewhere on the board
USART1RX: D1.102 (PA10); also elsewhere on the board
USART1TX: D1.101 (PA9); also elsewhere on the board
USART3RX: D1.78 (PD9), X9.2
USART3TX: D1.77 (PD8), X9.3

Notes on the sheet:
SPI1
I2C ADDR: 1001000 (48H)
I2C ADDR: 0011000 (18H)
ADC3_IN9 ADC3_IN14 ADC3_IN15 TIM10_CH1 TIM11_CH1 TIM13_CH1 TIM14_CH1
TIM9_CH1 TIM9_CH2
SPI2
SPI3
I2C1
TIM4_CH1
TIM4_CH2
USART2
USART1
USART3
V1.00
TELAKONE OHJAIN

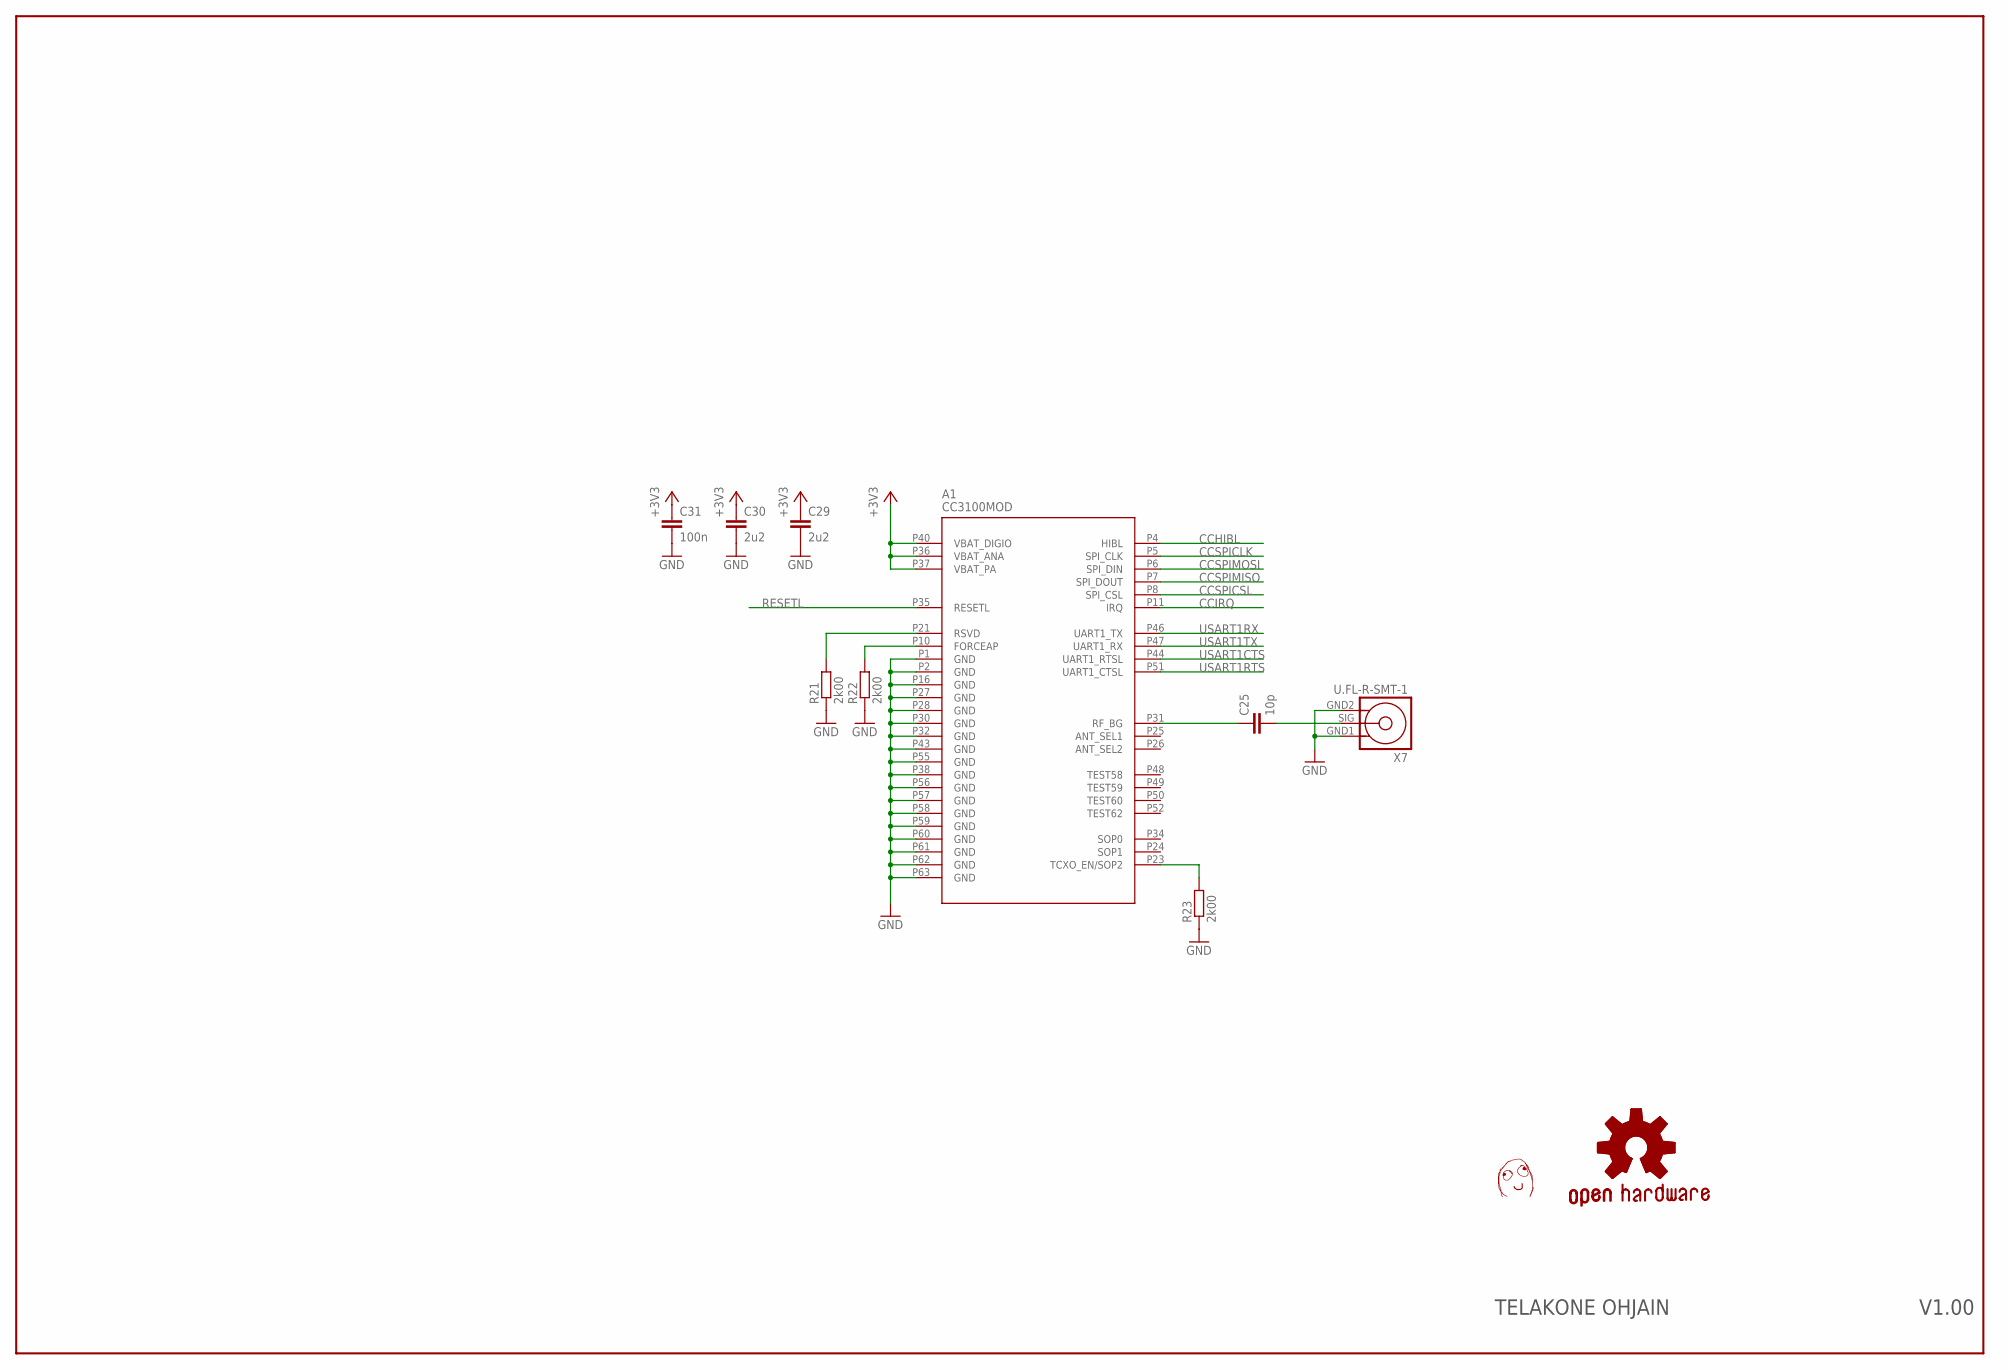
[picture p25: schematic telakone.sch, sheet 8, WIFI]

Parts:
A1: CC3100MOD
C25: 10p; C0603
C29, C30: 2u2; C0603
C31: 100n; C0603
R21, R22, R23: 2k00; R0603
U$15: DAFUG
X7: U.FL-R-SMT-1

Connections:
+3V3: A1.P36 (VBAT_ANA), A1.P37 (VBAT_PA), A1.P40 (VBAT_DIGIO), C29.1, C30.1, C31.1; also elsewhere on the board
CCHIBL: A1.P4 (HIBL); also elsewhere on the board
CCIRQ: A1.P11 (IRQ); also elsewhere on the board
CCSPICLK: A1.P5 (SPI_CLK); also elsewhere on the board
CCSPICSL: A1.P8 (SPI_CSL); also elsewhere on the board
CCSPIMISO: A1.P7 (SPI_DOUT); also elsewhere on the board
CCSPIMOSI: A1.P6 (SPI_DIN); also elsewhere on the board
GND: A1.P1 (GND), A1.P2 (GND), A1.P16 (GND), A1.P27 (GND), A1.P28 (GND), A1.P30 (GND), A1.P32 (GND), A1.P38 (GND), A1.P43 (GND), A1.P55 (GND), A1.P56 (GND), A1.P57 (GND), A1.P58 (GND), A1.P59 (GND), A1.P60 (GND), A1.P61 (GND), A1.P62 (GND), A1.P63 (GND), C29.2, C30.2, C31.2, R21.1, R22.1, R23.1, X7.GND1 (1), X7.GND2 (3); also elsewhere on the board
unnamed: A1.P31 (RF_BG), C25.1
unnamed: C25.2, X7.SIG (2)
unnamed: A1.P21 (RSVD), R21.2
unnamed: A1.P10 (FORCEAP), R22.2
unnamed: A1.P23 (TCXO_EN/SOP2), R23.2
RESETL: A1.P35 (RESETL); also elsewhere on the board
USART1CTS: A1.P44 (UART1_RTSL); also elsewhere on the board
USART1RTS: A1.P51 (UART1_CTSL); also elsewhere on the board
USART1RX: A1.P46 (UART1_TX); also elsewhere on the board
USART1TX: A1.P47 (UART1_RX); also elsewhere on the board

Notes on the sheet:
V1.00
TELAKONE OHJAIN

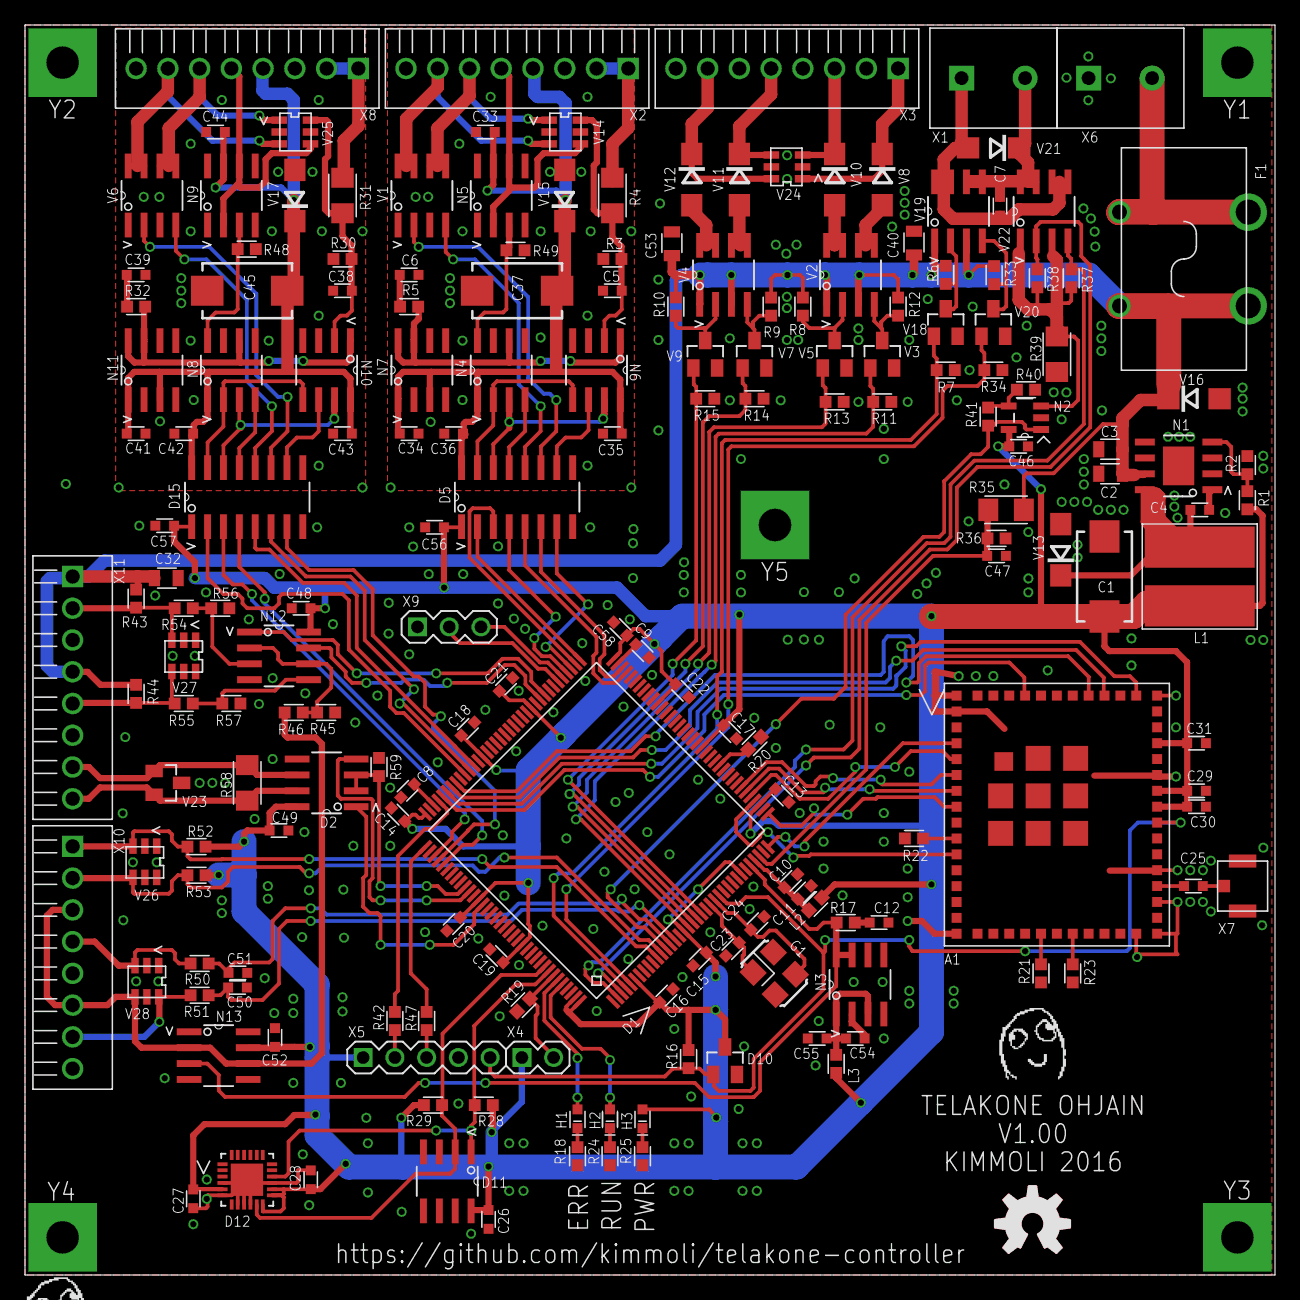
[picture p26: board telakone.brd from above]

Board: 2 copper layers, 100.0 x 100.0 mm, 196 parts (0 on the bottom side), 137 nets.

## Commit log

2016-09-17 initial eagle designs
    [telakone.brd, telakone.sch]
2016-09-17 p-fet outputs
    [telakone.brd, telakone.sch]
2016-09-18 placement sketching, temp and acceleration sensors, 2nd drive group
    [telakone.brd, telakone.sch]
2016-09-18 joystick inputs, change motor driver to plain fets, motor current measurement
    [telakone.brd, telakone.sch]
2016-09-19 schematic pdf
2016-09-19 add some protection
    [telakone.brd, telakone.sch]
2016-09-20 Schematics tuning
    Series resistors to SWDIO/SWCLK
    Pulldown to DAC outputs (HighZ after powerup)
    Some missing values added
    [telakone.brd, telakone.sch]
2016-09-21 speed sensor inputs
    [telakone.brd, telakone.sch]
2016-09-22 add accessory link 485 transceiver
    [telakone.brd, telakone.sch]
2016-09-24 placement, all on board
    [telakone.brd, telakone.sch]
2016-09-24 isolation groups routed
    [telakone.brd, telakone.sch]
2016-09-25 work commit, routing in progress
    [telakone.brd, telakone.sch]
2016-09-25 work commit, routing in progress, less than 100 to go :beer:
    [telakone.brd, telakone.sch]
2016-09-25 fully routed
    [telakone.brd, telakone.sch]
2016-09-25 Layout finished
    [telakone.brd, telakone.sch]
2016-09-25 small fixes
    [telakone.brd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]
2016-09-30 add version label to board
    [telakone.brd, telakone.sch]
2016-09-30 update documentation
    [telakone.brd, telakone.sch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]
2016-10-03 update component values, add bom
    [telakone.brd, telakone.sch]
2016-10-21 board photo
